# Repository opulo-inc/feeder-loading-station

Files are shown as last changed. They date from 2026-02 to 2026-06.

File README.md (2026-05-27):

# Feeder Loading Station

The Feeder Loading Station is an accessory used to help load electronic component tape into LumenPnP Feeders.

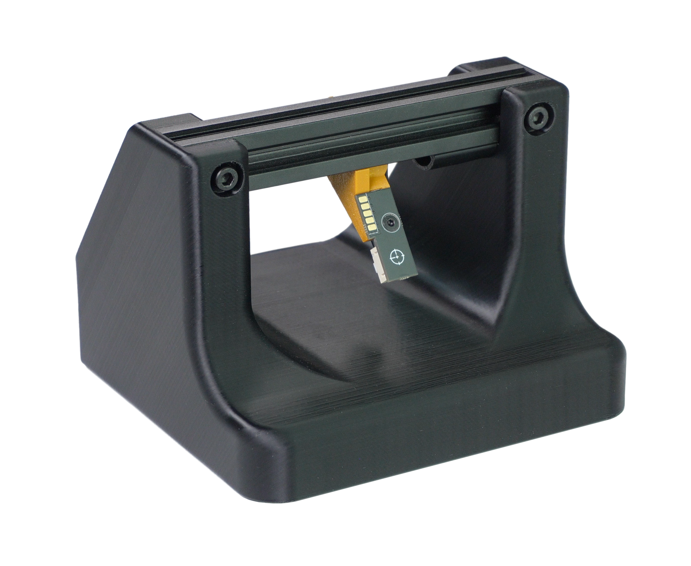
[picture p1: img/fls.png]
Feeder Loading Station


The FLS is effectively a short length of extrusion with a powered slot, used to provide a dedicated station to power the feeder while loading in component tape. It accepts a standard 24v barrel jack (same as what's used with the LumenPnP) and provides power to the single slot on the rail.

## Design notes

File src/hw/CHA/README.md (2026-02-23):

Generating Wireviz Drawings

1. Install `uv` if you haven't already:

    ```
    curl -LsSf https://astral.sh/uv/install.sh | sh
    ```

2. In terminal, cd into the CHA folder.

3. Run:

    ```
    uv venv
    uv sync
    ```

4. You now have wireviz installed in this folder. You can generate wirevis drawings from source using:

    ```
    uv run wireviz example-cable/example-cable.yml
    ```

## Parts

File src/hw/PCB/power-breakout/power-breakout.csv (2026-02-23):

Reference | Qty | Value | DNP | Exclude from BOM | Exclude from Board | Footprint | Datasheet | LCSC
C1,C3,C4,C5,C6 | 5 | 10u |  |  |  | Capacitor_SMD:C_0805_2012Metric |  | C440198
C2 | 1 | 100n |  |  |  | Capacitor_SMD:C_0805_2012Metric |  | C38141
D1 | 1 | SMF28A |  |  |  | Diode_SMD:D_SMF | https://www.vishay.com/doc?85881 | C2943742
D2,D3 | 2 | BZT52C16 |  |  |  | Diode_SMD:D_SOD-123 | https://diotec.com/tl_files/diotec/files/pdf/datasheets/bzt52b2v4.pdf | C216724
D4 | 1 | Green |  |  |  | LED_SMD:LED_0805_2012Metric |  | C965815
F1 | 1 | Fuse |  |  |  | Fuse:Fuseholder_Littelfuse_Nano2_154x | https://www.littelfuse.com/products/fuse-blocks-fuseholders-and-fuse-accessories/fuse-blocks/154/154005_dr.aspx | C206916
J1 | 1 | COMBO_POWER_JACK |  |  |  | index:BarrelJack_Horizontal | ~ | C5155559
J2 | 1 | Conn_01x04_Pin |  |  |  | Connector_JST:JST_PH_S4B-PH-SM4-TB_1x04-1MP_P2.00mm_Horizontal | ~ | C2845444
L1 | 1 | 2.2u |  |  |  | Inductor_SMD:L_Sunlord_MWSA0402S | ~ | C408335
R1,R4,R5 | 3 | 10k |  |  |  | Resistor_SMD:R_0805_2012Metric | ~ | C115295
R2,R3 | 2 | 4.7k |  |  |  | Resistor_SMD:R_0805_2012Metric | ~ | C17673
TP1,TP2,TP3 | 3 | TestPoint |  |  |  | TestPoint:TestPoint_Pad_D2.0mm | ~
U1,U2 | 2 | FDS4435BZ |  |  |  | Package_SO:SO-8_3.9x4.9mm_P1.27mm |  | C23931

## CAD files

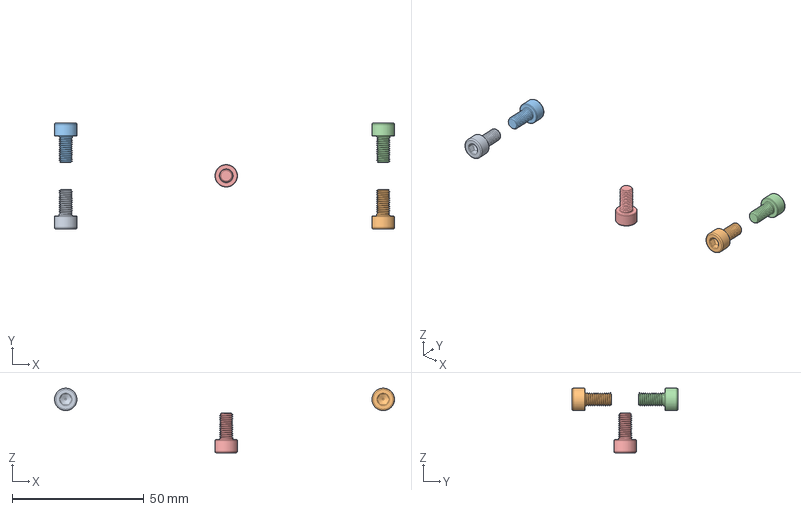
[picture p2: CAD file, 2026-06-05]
src/asm.FCStd
128.8 x 40.2 x 24.5 mm
M5x10-Screw013
M5x10-Screw015
M5x10-Screw017
M5x10-Screw019
M5x10-Screw021

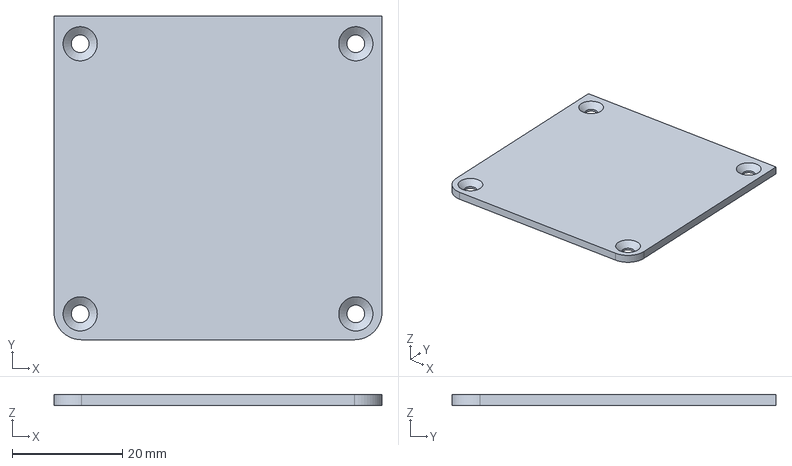
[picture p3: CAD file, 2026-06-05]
src/hw/FDM/fls-cover.FCStd
59.5 x 58.7 x 2.00 mm

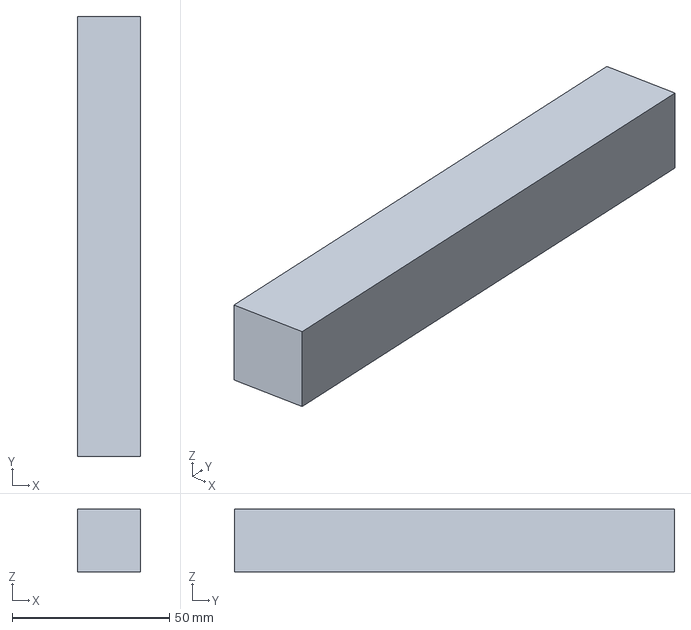
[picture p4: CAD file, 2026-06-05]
src/hw/OTS/vslot-extrusion-20mmx20mmx140mm.FCStd
20.0 x 140.0 x 20.0 mm

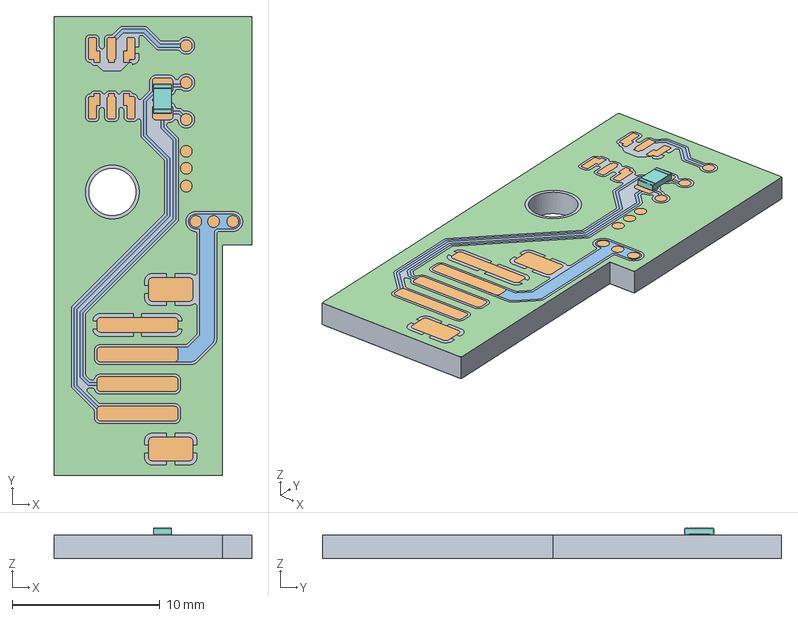
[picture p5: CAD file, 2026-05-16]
src/hw/PCB/feeder-slot/feeder-slot.FCStd
13.4 x 31.1 x 2.07 mm
Pcb_606d
topPads_606d
topTracks_606d
topZones_606d
botPads_606d
botTracks_606d
botZones_606d
R1_R_0805_2012Metric_87ce4d417120

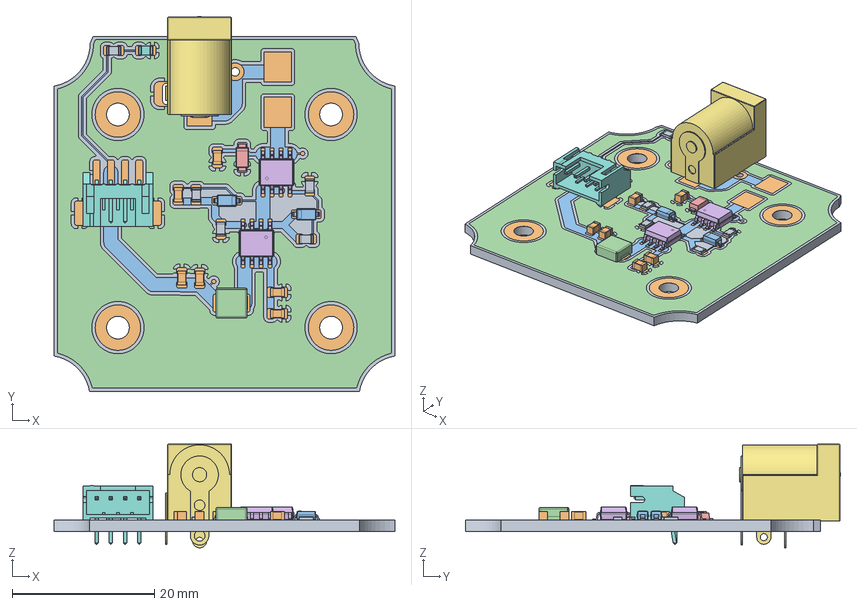
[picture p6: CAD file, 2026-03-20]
src/hw/PCB/power-breakout/power-breakout.FCStd
48.0 x 52.8 x 14.6 mm
Pcb_a5d3
topPads_a5d3
topTracks_a5d3
topZones_a5d3
botPads_a5d3
botTracks_a5d3
botZones_a5d3
D4_LED_0805_2012Metric_5e7533c20994
R3_R_0805_2012Metric_d935a907877d x 5
C3_C_0805_2012Metric_e1b4e1bd100a x 6
D2_D_SOD-123_0df1ad71775d x 2
L1_L_Sunlord_MWSA0402S_e6af32fb3148
D1_D_SMF_41abfd71dee5
U2_SO-8_3.9x4.9mm_P1.27mm_1f8cd4cd678f x 2
J1_BarrelJack_Horizontal_5ce78c207f45
J2_JST_S4B_PH_K_74297899fd63[2]

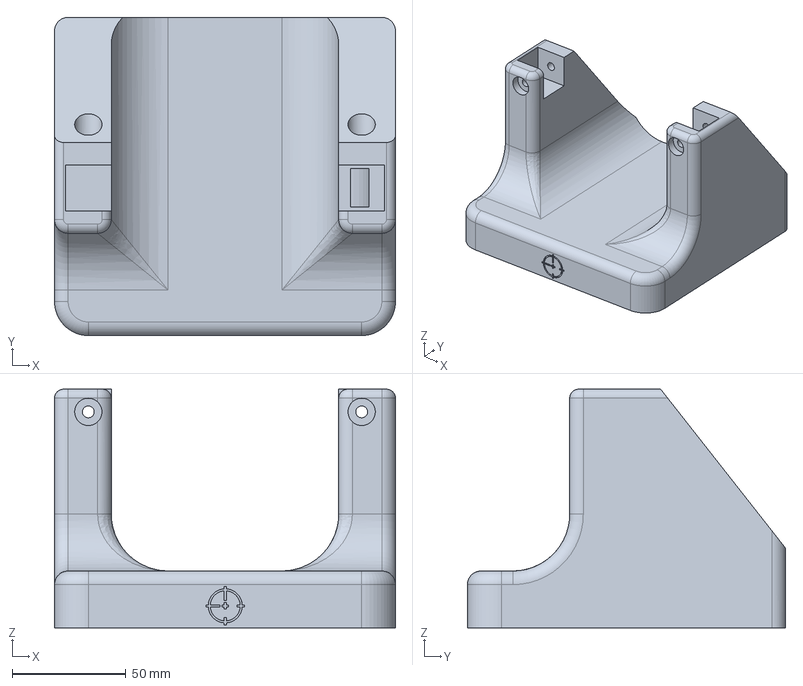
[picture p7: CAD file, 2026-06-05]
src/hw/FDM/fls-base.FCStd
150.0 x 140.0 x 105.0 mm

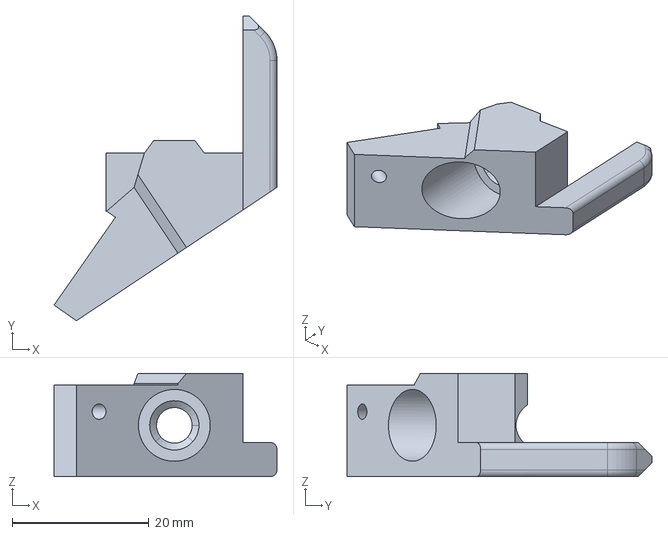
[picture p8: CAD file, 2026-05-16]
src/hw/FDM/slot-bracket.FCStd
32.6 x 44.5 x 15.1 mm

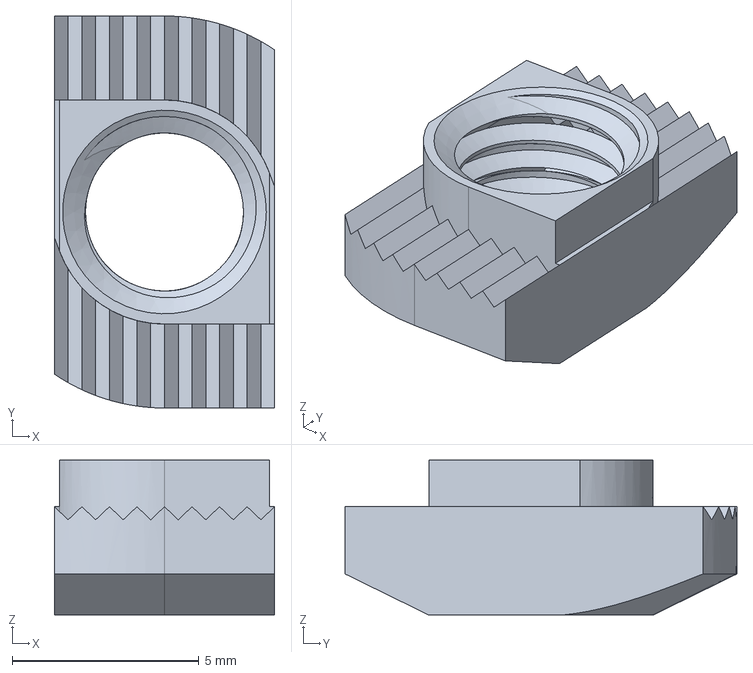
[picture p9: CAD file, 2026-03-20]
src/hw/OTS/M5-tslot-nut.FCStd
5.90 x 10.5 x 4.15 mm

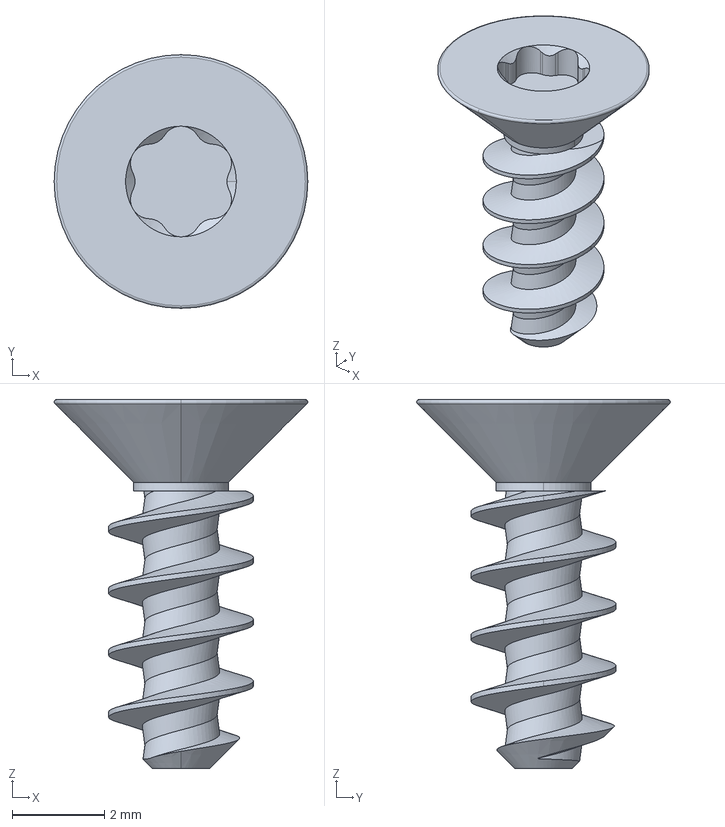
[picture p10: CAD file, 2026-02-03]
src/hw/OTS/m3x8mm-self-tapping-flat-hex-head.FCStd
5.50 x 5.50 x 8.00 mm

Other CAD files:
cad/FDM/asm.FCStd

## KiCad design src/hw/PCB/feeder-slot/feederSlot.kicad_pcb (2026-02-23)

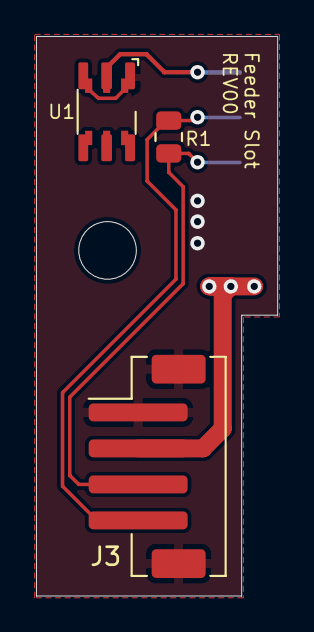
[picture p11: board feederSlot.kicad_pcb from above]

Board: 2 copper layers, 13.4 x 31.1 mm, 5 parts (1 on the bottom side), 5 nets.

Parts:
H1: MountingHole; MountingHole_3.2mm_M3
J2: Conn_01x05_Female; AVX-915-005-541-Contact-Surface
J3: Conn_01x04_Pin; JST_PH_B4B-PH-SM4-TB_1x04-1MP_P2.00mm_Vertical
R1: 120R; R_0805_2012Metric
U1: DS28E07; DS28E07_MULTI

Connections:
1WIRE: J2.1, U1.2 (IO)
GND: J2.4, J3.1, J3.MP, U1.1 (GND)
RS-485+: J2.2, J3.4, R1.2
RS-485-: J2.3, J3.3, R1.1
VIN: J2.5, J3.2

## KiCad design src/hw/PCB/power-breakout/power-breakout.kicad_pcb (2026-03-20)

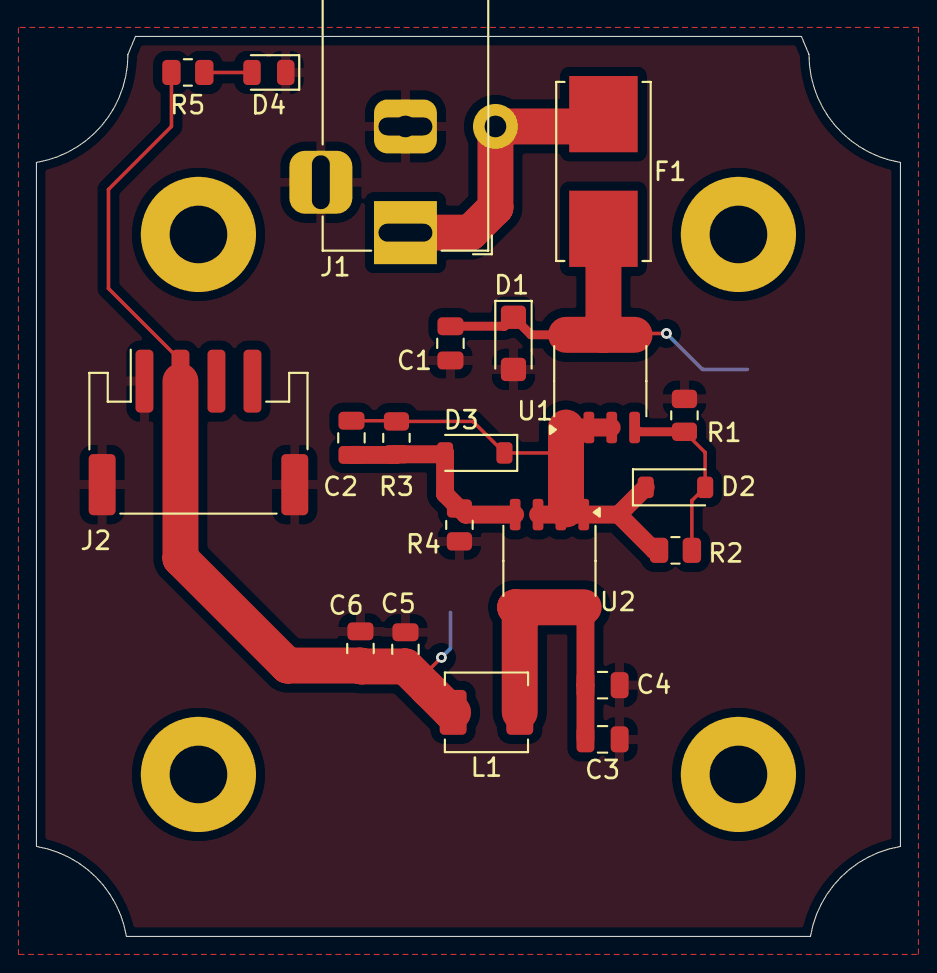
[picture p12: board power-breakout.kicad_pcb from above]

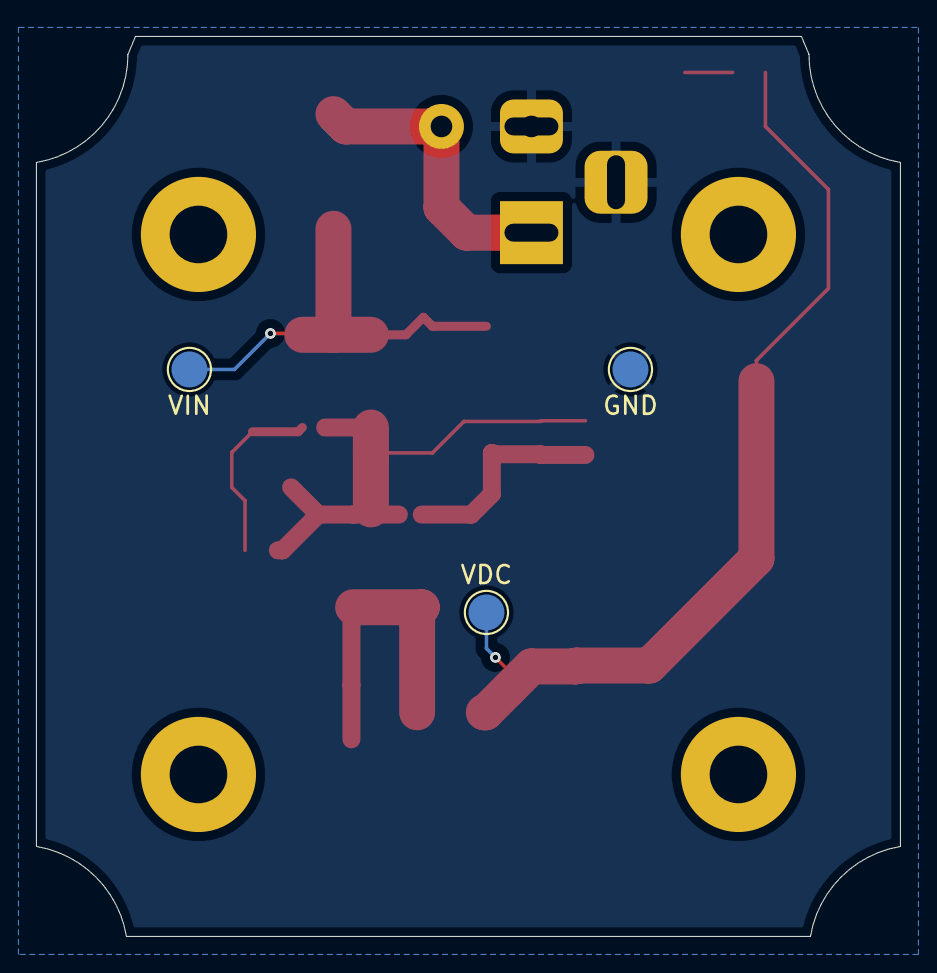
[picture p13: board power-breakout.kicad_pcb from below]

Board: 2 copper layers, 48.0 x 50.0 mm, 24 parts (3 on the bottom side), 9 nets.

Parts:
C1, C3, C4, C5, C6: 10u; C_0805_2012Metric
C2: 100n; C_0805_2012Metric
D1: SMF28A; D_SMF
D2, D3: BZT52C16; D_SOD-123
D4: Green; LED_0805_2012Metric
F1: Fuse; Fuseholder_Littelfuse_Nano2_154x
GND: TestPoint; TestPoint_Pad_D2.0mm
J1: COMBO_POWER_JACK; BarrelJack_Horizontal
J2: Conn_01x04_Pin; JST_PH_S4B-PH-SM4-TB_1x04-1MP_P2.00mm_Horizontal
L1: 2.2u; L_Sunlord_MWSA0402S
R1, R4, R5: 10k; R_0805_2012Metric
R2, R3: 4.7k; R_0805_2012Metric
U1, U2: FDS4435BZ; SO-8_3.9x4.9mm_P1.27mm
VDC: TestPoint; TestPoint_Pad_D2.0mm
VIN: TestPoint; TestPoint_Pad_D2.0mm

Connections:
/POWER_SUPPLY: F1.1, J1.1, J1.4
/VIN: C1.2, D1.1 (A1), F1.2, U1.5 (D), U1.6 (D), U1.7 (D), U1.8 (D), VIN.1
GND: C1.1, C3.1, C4.1, C5.1, C6.1, D1.2 (A2), D4.1 (K), GND.1, J1.2, J1.3, J2.1, J2.MP, R1.2, R4.2
unnamed: C3.2, C4.2, L1.1, U2.5 (D), U2.6 (D), U2.7 (D), U2.8 (D)
unnamed: D2.2 (A), R1.1, R2.2, U1.4 (G)
unnamed: C2.2, D2.1 (K), D3.1 (K), R2.1, R3.1, U1.1 (S), U1.2 (S), U1.3 (S), U2.1 (S), U2.2 (S), U2.3 (S)
unnamed: C2.1, D3.2 (A), R3.2, R4.1, U2.4 (G)
unnamed: D4.2 (A), R5.2
VDC: C5.2, C6.2, J2.2, L1.2, R5.1, VDC.1

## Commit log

2026-02-03 updates .gitignore
    [asm.FCStd, base.FCStd, cover.FCStd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]
2026-02-03 updates base to have corrected cable channel, reorgs files
    [asm.FCStd, base.FCStd, frame.FCStd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]
2026-02-03 updates cable length to the correct 300mm
    [asm.FCStd, base.FCStd, cover.FCStd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]
2026-02-03 updates asm, adds proper self-tapping screw
    [asm.FCStd, m3x8mm-self-tapping-flat-hex-head.FCStd, rail.FCStd]
2026-02-18 updates part source for breakout, updates silkscreen
    [power-breakout.kicad_pcb, power-breakout.kicad_sch]
2026-02-23 updates placement for silk on feeder-slot
    [feederSlot.kicad_pcb, feederSlot.kicad_sch, power-breakout.csv]
2026-03-20 adds slot pcb, updates asm, updates slot bracket
    [asm.FCStd, feeder-slot.FCStd, slot-bracket.FCStd]
2026-04-29 updates slot bracket
    [slot-bracket.FCStd]
2026-05-16 opens up slot for extrusion a bit for an easier fit, adds icon, adds recesses for rubber feet alignment
    [asm.FCStd, feeder-slot.FCStd, fls-base.FCStd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]
2026-05-27 this commit represents PVT-01
    [fls-base.FCStd]
2026-05-27 release prep
    [M5-tslot-nut.FCStd, feeder-slot.FCStd, feederSlot.kicad_pcb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]
2026-06-05 cleans up assembly
    [asm.FCStd, fls-base.FCStd, fls-cover.FCStd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]
